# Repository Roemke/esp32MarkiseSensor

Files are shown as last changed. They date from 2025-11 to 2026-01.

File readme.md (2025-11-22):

# Markisensensoren
Ein wenig was zur schaltung

# Schaltung Windsensor
den habe ich noch nicht:
Dieser liefert 20 Pulse pro s bei 1,75m/s
wind, viel mit chatgpt gespielt, er liefert teilweise widersprüchliche

Schaltpläne, daher hier nochmal die mir sinnvoll erscheinende Variante
Windsensor: https://www.amazon.de/dp/B0872XPWFC?ref=ppx_yo2ov_dt_b_fed_asin_title
Mumusuki 0-70 m/s Umgebungssignal Ausgang Impulstyp Kohlenstoff 
Windgeschwindigkeitssensor Anemometer DREI Tassen Sender Windgeschwindigkeitssensor 

Erfahrung mit chat-GPT zur Schaltungskonzeption. Solange es um
Textbeschreibungen geht, hört es sch vernünftig an, wenn er daraus 
Schaltpläne macht (Ascii oder PNG) kommt ziemlich viel Müll heraus. 
Der folgende Plan müsste sinnvoll sein

```text
3.3V
     |
    4.7k  <-- Pull-up (zieht Signal auf 3.3V)
     |
     +------ Node_Signal ----+------> [1k] ----> GPIO (ESP32)
     |                      |
     |                     (optional)
     |                      | 
   Sensor OUT (open-col.)   --- C = 10 nF
     blau                   --- 
                            |
                            GND
```
Windsensor braucht 5-30 V separat und gemeinsame Masse mit ESP

Erläuterungen / wichtige Punkte

    Node_Signal ist der gemeinsame Punkt, an dem Pull-up, Sensor-OUT und Kondensator zusammentreffen.

    Sensor OUT ist open-collector / NPN: wenn aktiv → Node wird auf GND gezogen (LOW). 
    Wenn inaktiv → Pull-up zieht Node auf 3.3 V (HIGH).

    1 kΩ sitzt zwischen Node und dem ESP-GPIO (physisch nahe am ESP-Pin angebracht). 
    Er schützt den GPIO bei Fehlverdrahtung oder wenn der Pin versehentlich als Ausgang konfiguriert ist.

    C = 10 nF (optional) zwischen Node_Signal und GND dicht am ESP-Eingang: entstört sehr kurzzeitige Störungen, 
    aber klein genug, um keine 800 Hz-Impulse zu verschlucken (mit 4.7k → τ ≈ 47 µs).
    (Keramik-Kondensator)

    Gemeinsame Masse: Sensor-GND und ESP-GND unbedingt verbinden.

Strom-/Pegelrechnung (zur Sicherheit)

    Wenn Sensor LOW zieht: Strom durch Pull-up ≈ 3.3 V / 4.7 k ≈ 0.7 mA → unkritisch.

    Wenn aufgrund Boot/Fehlkonfig ein Pegelkonflikt entsteht (ESP Pin OUTPUT HIGH = 3.3 V, Sensor zieht auf GND), 
    begrenzt 1 k den Strom grob auf ~3.3 mA → schützt den Pin. (vorher war
    auch von Blitz und elektromagnetschen Störungen die Rede

Ich habe in Erinnerung, dass ich GPIO 33 gewählt habe. 

## Reedschalter Markise 
Die Reed-Schalter für die Markise (GPIO 26 m, 25 s1 und 27 s2)

Sie sind folgender Typ: 
https://www.amazon.de/dp/B07Z4NCWDD?ref=ppx_yo2ov_dt_b_fed_asin_title&th=1
normally closed, d.h. der magnet schließt das system (chat gpt sieht die
Bezeichnung genau anders herum) 

Schaltung ist vom GPIO 100nF Keramik auf GND (Entstörung) direkt am ESP pin
und 470Ohm in Serie im Signalleiter, als Schutz.
(bei der Windgeschichte ist es anders, da kommt erst der 1k Widerstand dann
der kondensator (vom esp aus gesehen), eine analyse durch chat gpt sagt aber
das auch dies ok ist, wobei bei der Windschaltung ja auch nicht der interne
pullup genutzt wird.
 
Hier wird kein externer pullup eingesetzt, da der Interne reicht. Dieser ist
relativ hochohmig 40-50k und zieht daher den GPIO nur langsam auf high, das
macht bei den Reeds für die markise aber nichts 

## Temperatur Luftfeuchtigkeit

Und dann noch ein dht22 engebaut in am2302 (hat nur 3 Beinchen) für
Temperatur und Luftfeuchtigkeit, ist direkt an GPIO angeschlossen (GPIO23)
und an 3.3V vom ESP

Stromversorgung ESP über USB, ansonsten alles auf einer Lochrasterplatine. 
Es würde sich aber ein PCB lohnen.

## Stand
Lötarbeiten auch für den Windsensor sind soweit durch. Blau für Signale der
Reedkontakte und des Temperatursensors verwendet, grün für Windsensor.
Alles auf Lochraster, schon eine ziemliche Bastelei, hier hätte sich ein
Platinendesign gelohnt, also machen, wenn es nicht stabil läuft.
Na ob ich dazu noch Lust habe? Die Verkabelung nach außen über Wagoklemmem
gemacht, es sind halt jetzt doch einige, eigenes kleines Gehäuse
3mal Reed - in 2er
3.3 V  - in 2er
Temp   - in 2er
Signal Wind - in 2er 
12 V   - in 3er (an Spannungswandler auf 5 V für Esp / an Windsensor / Eingang
Masse  - jede Menge, ich hoffe ich habe alles, an 5er Wago

den Temp-Sensor in eigenes kleines gehäuse, nicht gut, aber egal, kein Aufwand 
betreiben, der Sensor wird schon 1-2 Jahre halten :-), habe aber schwarzes pla genommen, bei
Sonne wird er gut warm werden...

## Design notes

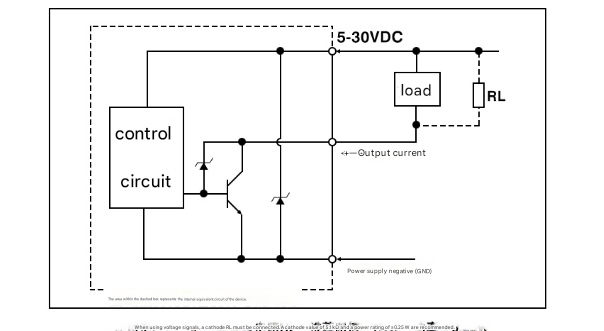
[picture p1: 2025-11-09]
SchaltplanNPN.png

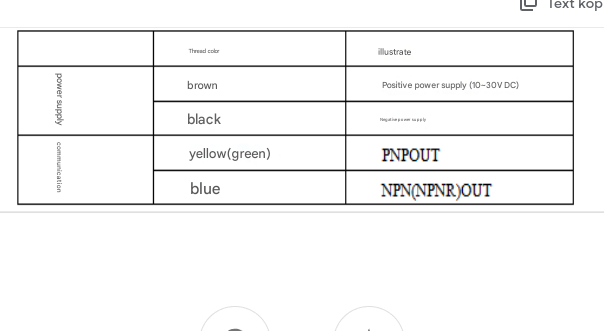
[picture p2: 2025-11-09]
WindsensorBelegung.png

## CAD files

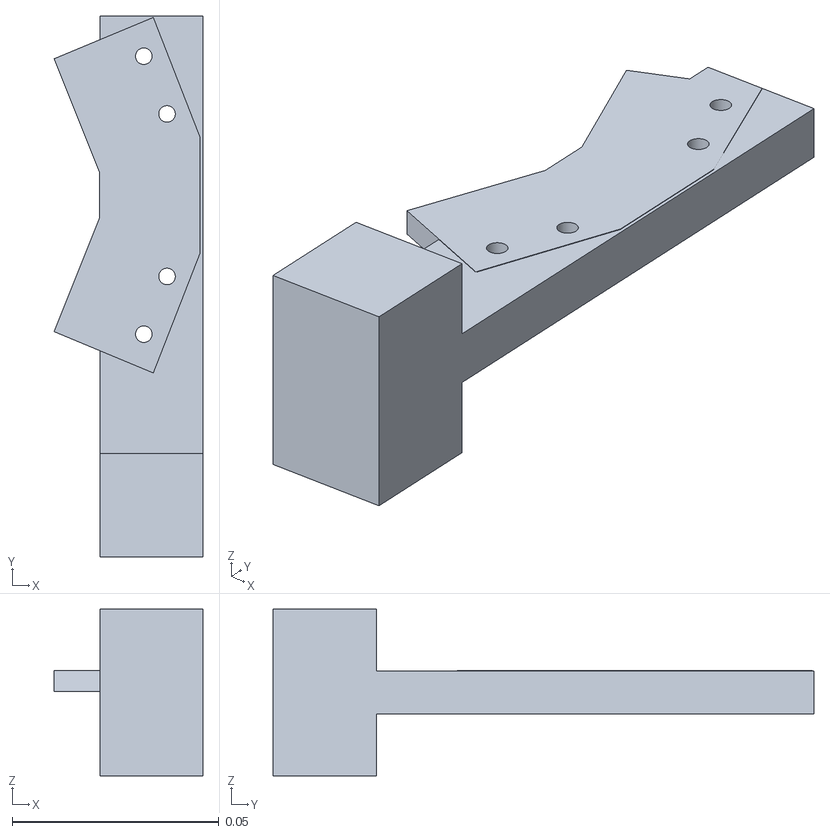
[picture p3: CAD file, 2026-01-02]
magnetHalter.stl
0.036 x 0.131 x 0.0404

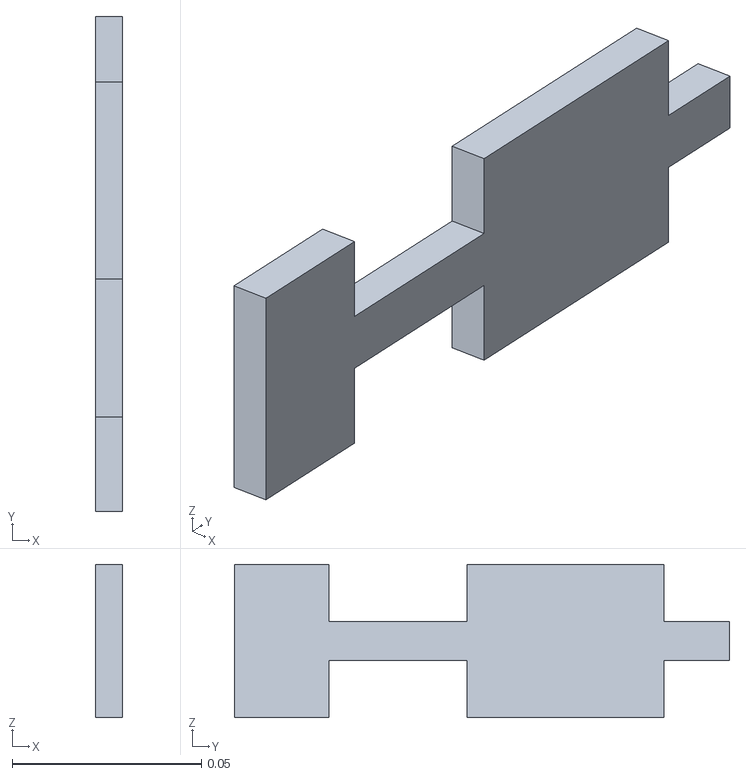
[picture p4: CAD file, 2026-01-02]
magnetHalterPlatte.stl
0.00703 x 0.131 x 0.0404

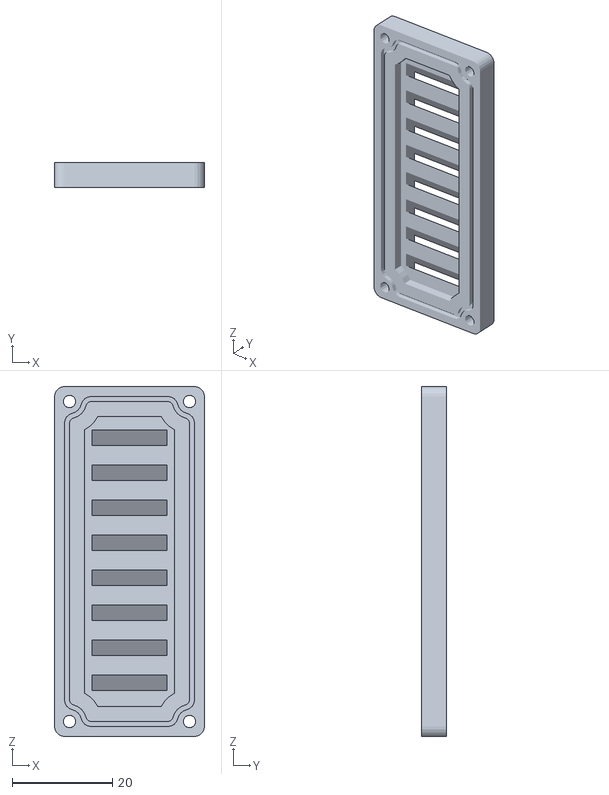
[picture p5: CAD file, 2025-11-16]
housing_sendor_dht22_cover.stl
30.0 x 5.00 x 70.0

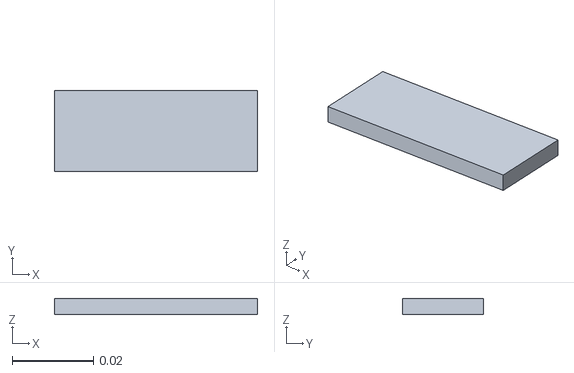
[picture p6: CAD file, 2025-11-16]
plate.stl
0.05 x 0.02 x 0.004

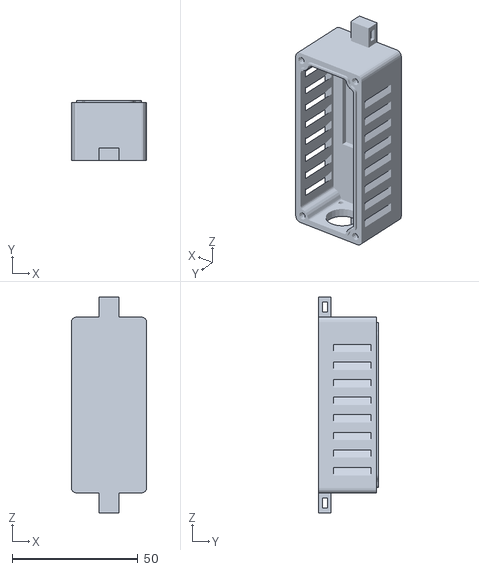
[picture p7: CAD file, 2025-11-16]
housing_sendor_dht22_body_outdoor_pg7.stl
30.0 x 23.9 x 86.0

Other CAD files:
magnetHalter.blend
plate.blend

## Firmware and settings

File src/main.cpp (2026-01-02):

//main.cpp

//#include <EEPROM.h> umgestellt auf littlefs
// Eigene Header
//#include "credentials.h" //fuer zuhause, eigentlich überflüssig mit wifi.h
#include "main.h"
#include "indexHtmlJS.h"
#include "wifi.h"
#include "logging.h"
#include "mqtt.h"
// Problem - chatgpt: 
// Du sendest WebSocket-Nachrichten (ws.textAll()) während eines WebSocket-Events.
//hmm, hätte ich auch selber drauf kommen können...?
// müsste ich ggf. auch in anderen Projekten anpassen...
bool pendingReboot = false;
bool insideWebSocketEvent = false;
//gleiches Problem bei informClients (json-kram)
std::vector<PendingWSMsg> wsOutbox;

// ---- WebServer + WebSocket ----
AsyncWebServer server(80);
AsyncWebSocket ws("/ws");
// DHT22 (AM2302)
DHTesp dht;
bool dhtReady = false;
float curTemp = NAN, curHum = NAN;
uint32_t lastDhtMs = 0;
static const char* REED_CFG_PATH = "/reed.json";


//fuer die reedPins
struct ReedPins {
  int markise = 26; // Defaults
  int s1 = 25;
  int s2 = 27; 
  int wind = 33;
  int t = 23;   // Temperatur, kein Reed, aber speichern
} reedPins;

//windgeschichten
volatile uint32_t windPulses = 0;   // Zählt die Pulse per ISR, volatile wegen ISR

float windSpeed = 0.0f; 

void IRAM_ATTR windISR() { //darf nicht inline sein
  windPulses++;
}

bool pollWindSensor() 
{
    static float lastWind = NAN;
    static uint32_t lastPoll = 0;

    uint32_t now = millis();
    if (now - lastPoll < 500) return false; // alle 500 ms
    lastPoll = now;

    // Pulse atomar lesen und zurücksetzen
    uint32_t pulses = windPulses;
    windPulses = 0;

    // 500ms → factor 2
    float pps = pulses * 2.0f;
    float newWind = pps * (1.75f / 20.0f);

    bool changed = false;
    if (isnan(lastWind) || fabsf(newWind - lastWind) >= 0.1f) {  
        // Änderung >= 0.1 m/s
        changed = true;
    }

    windSpeed = newWind;
    lastWind = newWind;

    if (changed) {
        logPrintf("Wind geändert: %.2f m/s\n", windSpeed);
    }

    return changed;
}


// Entprellung für Reedkontakte (aktiv LOW)
struct Debounce {
  int pin = -1;
  bool stable = false;   // entprellt (true = Reed geschlossen = LOW)
  bool lastRaw = false;
  uint32_t lastChange = 0;
  uint16_t debounceMs = 20;
} dbM, dbS1, dbS2;

static inline bool rawReed(int pin) { return digitalRead(pin) == LOW; }

bool updateDebounce(Debounce& d, uint32_t nowMs) {
  bool raw = rawReed(d.pin);
  bool changed = false;
  if (raw != d.lastRaw) { d.lastRaw = raw; d.lastChange = nowMs; }
  if ((nowMs - d.lastChange) >= d.debounceMs && d.stable != d.lastRaw) {
    d.stable = d.lastRaw;
    changed = true;
  }
  return changed;
}

// Sensor-Snapshot als JSON-String bauen
String makeSensorMsg() {
  JsonDocument doc;
  doc["action"] = "sensor";
  JsonObject v = doc["value"].to<JsonObject>();
  if (!isnan(curTemp)) v["t"] = curTemp;
  if (!isnan(curHum))  v["h"] = curHum;
  v["m"]  = (int)dbM.stable;
  v["s1"] = (int)dbS1.stable;
  v["s2"] = (int)dbS2.stable;
  v["w"]  = roundf(windSpeed * 10) / 10.0f;
  String msg;
  serializeJson(doc, msg);
  return msg;
}


static bool isSafeInputPullupPin(int gpio) {
  // verbotene Gruppen
  if (gpio >= 6 && gpio <= 11) return false;  // Flash
  if (gpio >= 34 && gpio <= 39) return false;  // keine internen Pullups
  if (gpio == 0 || gpio == 2 || gpio == 12 || gpio == 15) return false; // Boot-Straps
  // ansonsten ok (0..39)
  return gpio >= 0 && gpio <= 39;
} 
bool reedSaveConfig() {
  File f = LittleFS.open(REED_CFG_PATH, "w");
  if (!f) return false;
  JsonDocument doc;
  doc["markise"] = reedPins.markise;
  doc["s1"] = reedPins.s1;
  doc["s2"] = reedPins.s2;
  doc["t"] = reedPins.t;
  doc["wind"] = reedPins.wind;
  bool ok = (serializeJson(doc, f) > 0);
  f.close();
  return ok;
}

bool reedLoadConfig() {
  if (!LittleFS.exists(REED_CFG_PATH)) {
    // Defaults erstmal speichern
    return reedSaveConfig();
  }
  File f = LittleFS.open(REED_CFG_PATH, "r");
  if (!f) return false;
  JsonDocument doc;
  auto err = deserializeJson(doc, f);
  f.close();
  if (err) return false;

  int m = doc["markise"] | reedPins.markise;
  int s1 = doc["s1"] | reedPins.s1;
  int s2 = doc["s2"] | reedPins.s2;
  int t = doc["t"] | reedPins.t;
  int w = doc["wind"] | reedPins.wind;

  // Validieren
  if (isSafeInputPullupPin(m)) reedPins.markise = m;
  if (isSafeInputPullupPin(s1)) reedPins.s1 = s1;
  if (isSafeInputPullupPin(s2)) reedPins.s2 = s2;
  if (isSafeInputPullupPin(t)) reedPins.t = t;
  if (isSafeInputPullupPin(w)) reedPins.wind = w;
  return true;
}

void reedApplyPins() {
  pinMode(reedPins.markise, INPUT_PULLUP);
  pinMode(reedPins.s1, INPUT_PULLUP);
  pinMode(reedPins.s2, INPUT_PULLUP);
  pinMode(reedPins.t, INPUT);
  pinMode(reedPins.wind, INPUT); //externer Pullup
  attachInterrupt(reedPins.wind, windISR, FALLING);//interrupt ISR bei fallender Flanke
  
}

static void mqttPublishAwning() {
  JsonDocument doc;
  bool closed = dbM.stable;                 // dein Reed M als „geschlossen/offen“
  doc["closed"] = closed;
  // optional: alte Namenskompatibilität
  doc["m"] = closed ? "geschlossen" : "offen";
  // optional: S1/S2 als binäre Readings
  doc["s1"] = dbS1.stable ? 1 : 0;
  doc["s2"] = dbS2.stable ? 1 : 0;
  // optional: Prozent p, falls Du sie berechnen kannst
  // doc["p"] = isnan(percent) ? nullptr : (int)lroundf(constrain(percent,0,100));

  String payload; 
  payload.reserve(96);
  serializeJson(doc, payload);
  mqtt.publishAwningStatus(payload);        // -> awning/status
}

static void mqttPublishClimate() {
  JsonDocument doc;
  if (isnan(curTemp)) doc["t"] = nullptr;
  else                doc["t"] = roundf(curTemp * 10) / 10.0f;

  if (isnan(curHum))  doc["h"] = nullptr;
  else                doc["h"] = roundf(curHum * 10) / 10.0f;

  // Wind (m/s)
  if (isnan(windSpeed)) doc["w"] = nullptr;
  else                  doc["w"] = roundf(windSpeed * 10) / 10.0f;

  String payload; 
  payload.reserve(128);
  serializeJson(doc, payload);
  mqtt.publishClimateStatus(payload);       // -> climate/status
}


//Prozessor um ggf. Werte zu setzen (webseite)
String processor(const String& var)
{
  String result = "";
 
  if (var == "COPYRIGHT")
    result = "2025 by Roemke";
  else if (var == "WIFI_MAC_AP")
    result = wifiMacAp;
  else if (var == "WIFI_MAC_STA")
    result = wifiMacSta;
  else if (var == "WIFI_MAC_MODE")
    result = wifiMode;
  else if (var == "MQTT_BROKER")
    result = mqtt.broker;
  else if (var == "MQTT_PORT")
    result = String(mqtt.port);
  else if (var == "GPIO_MARKISE")
    result = String(reedPins.markise);
  else if (var == "GPIO_S1")
    result = String(reedPins.s1);
  else if (var == "GPIO_S2")
    result = String(reedPins.s2);
  else if (var == "GPIO_T")
    result = String(reedPins.t);
  else if (var == "GPIO_WIND")
    result = String(reedPins.wind);
    
  return result;
}



// ---- WebSocket Event Handler ----
// Nachricht an alle Clients senden
template <typename T>
void informClients(const String& action, T value) 
{
  JsonDocument doc;
  doc["action"] = action;
  doc["value"] = value;   // JsonVariant nimmt String oder int

  String msg;
  serializeJson(doc, msg);
  wsOutbox.push_back({0, msg});
}


void initialInformClient(AsyncWebSocketClient *client)
{  
  JsonDocument doc;
  doc["action"] = "init";
  // Log-Array hinzufügen
  JsonArray logArr = doc["logs"].to<JsonArray>();
  for (uint8_t i = 0; i < logCount; i++) {
    uint8_t idx = (logIndex + LOG_BUFFER_SIZE - logCount + i) % LOG_BUFFER_SIZE;
    logArr.add(logBuffer[idx]);
  }
  String msg;
  serializeJson(doc, msg);
  wsOutbox.push_back({client->id(), msg});
  wsOutbox.push_back({client->id(), makeSensorMsg()});
}

void onWsEvent(AsyncWebSocket *server, AsyncWebSocketClient *client,
  AwsEventType type, void *arg, uint8_t *data, size_t len)
{  
  insideWebSocketEvent = true;
  if (type == WS_EVT_CONNECT) 
  {
    logPrintf("📡 Client #%u verbunden\n", client->id());
    // Aktuellen Status senden
    initialInformClient(client);
    insideWebSocketEvent = false;
    return;
  }
  if (type == WS_EVT_DISCONNECT) {
    insideWebSocketEvent = false;
    return;
  }
  if(type != WS_EVT_DATA) 
  {
    insideWebSocketEvent = false;
    return;
  }

  logPrintf("Event-Type: %d, Heap: %d\n", type, ESP.getFreeHeap());
  AwsFrameInfo *info = (AwsFrameInfo*)arg;

  // Debug aller Bedingungen
  if(!info->final) {
      logPrintf("❌ WS: info->final == false\n");
      insideWebSocketEvent = false;
      return;
  }

  if(info->index != 0) {
      logPrintf("❌ WS: info->index = %u (erwartet 0)\n", info->index);
      insideWebSocketEvent = false;
      return;
  }

  if(info->len != len) {
      logPrintf("❌ WS: info->len (%u) != len (%u) -> frame fragmentiert?\n",
                info->len, len);
      insideWebSocketEvent = false;
      return;
  }

  if(info->opcode != WS_TEXT) {
      logPrintf("❌ WS: opcode = %u (erwartet WS_TEXT=1)\n", info->opcode);
      insideWebSocketEvent = false;
      return;
  }

  logPrintf("✔️ WS: Frame OK – Verarbeitung laeuft weiter\n");

  // StaticJsonDocument mit ausreichendem Puffer, deprecated sollte reichen ein JsonDocument zu nehmen
  JsonDocument doc;
  DeserializationError error = deserializeJson(doc, data,len);
  if(error) 
  {
    Serial.print("JSON Fehler: ");
    logPrintln(error.c_str());
    insideWebSocketEvent = false;
    return;
  }

  String action = doc["action"] | "";
  JsonVariant value = doc["value"];
  String valueStr = value.isNull() ? "" : value.as<String>();
  logPrintf("Aktion: %s, Wert: %s\n", action.c_str(), valueStr.c_str());
   
  if (action == "wifiSetCredentials")
  {
      String ssid = value["ssid"] | "";
      String pass = value["password"] | "";
      logPrintf("Neue WiFi Daten: SSID=%s, PASS=%s\n", ssid.c_str(), pass.c_str());
      if (ssid.length() > 0)
      {
          wifiSetCredentials(ssid.c_str(), pass.c_str());
          informClients("wifiState", "saved");
          pendingReboot = true;          
      }
  }
  else if (action == "mqttSet")
  {
      String broker = value["broker"] | "";
      int port = value["port"] | 1883;
      logPrintf("Neue MQTT Daten: BROKER=%s, PORT=%d\n", broker.c_str(), port);
      if (broker.length() > 0)
      {
          mqtt.broker = broker;
          mqtt.port = port;
          mqtt.saveConfig();          
          // Kein Neustart notwendig, MQTT-Verbindung wird neu initialisiert
      }
  }
  else if (action == "reedSetPins") 
  {
    int m  = value["markise"] | reedPins.markise;
    int s1 = value["s1"]      | reedPins.s1;
    int s2 = value["s2"]      | reedPins.s2;
    int t = value["t"]      | reedPins.t;
    int w  = value["wind"] | reedPins.wind;

    // Validieren
    if (!isSafeInputPullupPin(m) || !isSafeInputPullupPin(s1) || !isSafeInputPullupPin(s2)) {
      informClients("error", "Ungueltige GPIOs (keine Pullups/Flash/Bootstraps)");
      insideWebSocketEvent = false;
      return;
    }
    // Vorherige Pins sind INPUT_PULLUP – keine Deinit nötig,
    // optional könnte man hier prüfen, ob Pins sich geändert haben.
    reedPins.markise = m;
    reedPins.s1 = s1;
    reedPins.s2 = s2;
    reedPins.t = t;
    reedPins.wind = w;
    
    reedApplyPins();
    reedSaveConfig();
    informClients("reedPinsSaved", "ok");
    logPrintf("GPIO Pins aktualisiert: M=%d, S1=%d, S2=%d, T=%d, W=%d\n", m, s1, s2,t,w);
  }
  else if (action == "reboot") 
  {
    logPrintln("Reboot Befehl empfangen, Neustart...");
    informClients("rebooting", "ESP wird neu gestartet");
    pendingReboot = true;        
  }
  else if (action == "check") 
  {
    String msg = valueStr.length() > 0 ? valueStr : "Testnachricht vom Client";
    logPrintf("Check-Nachricht empfangen: %s\n", msg.c_str());
    informClients("check", msg);
  }
  else if (action == "setMaxWind")
  {
      int mw = value.as<int>();//esp benötigt den Wert nicht, verteilt aber an die Clients
      logPrintf("MaxWind setzen auf: %d\n", mw);
      // Rückmeldung an alle Clients
      informClients("setMaxWind", mw);      
  }
  
  insideWebSocketEvent = false;
}

void setupDHTandSensor()
{
    // Debouncer initialisieren
    dbM.pin = reedPins.markise;
    dbS1.pin = reedPins.s1;
    dbS2.pin = reedPins.s2;
    uint32_t now = millis();
    dbM.lastRaw = dbM.stable = rawReed(dbM.pin);
    dbS1.lastRaw = dbS1.stable = rawReed(dbS1.pin);
    dbS2.lastRaw = dbS2.stable = rawReed(dbS2.pin);
    dbM.lastChange = dbS1.lastChange = dbS2.lastChange = now;
  
    // DHT22 (AM2302) starten
    dht.setup(reedPins.t, DHTesp::DHT22);
    dhtReady = true;    
}

void setupOTA() {
  ElegantOTA.begin(&server); // Startet ElegantOTA  
  
  ElegantOTA.onStart([]() {
    logPrintln("OTA Start");
  });

  ElegantOTA.onEnd([](bool success) {
    success ? logPrintln("OTA Ende, Neustart...") : logPrintln("OTA Ende mit Fehler");
    success ? ESP.restart() : logPrintln("Kein Neustart");   
  });

  ElegantOTA.onProgress([](unsigned int progress, unsigned int total) {
    char buf[64];
    snprintf(buf, sizeof(buf), "OTA Fortschritt: %u/%u", progress, total);
    logPrintln(buf);
    informClients("ota", buf);
  });
  
  logBufferAdd("🌐 OTA Update verfügbar unter /update");
}

void setupWebsocket()
{
  // WebSocket einbinden
  ws.onEvent(onWsEvent);
  server.addHandler(&ws);

  // lustig, ich bin alt,  [] leitet einen Lambda Ausdruck ein, also eine anonyme Funktion
  // die gabs frueher nicht :-), dafür mehr Lametta
  server.on("/favicon.ico", [](AsyncWebServerRequest *request)
            {
              request->send(204); // no content
            });

  // Hauptseite
  server.on("/", HTTP_GET, [](AsyncWebServerRequest *request)
            { request->send(200, "text/html", index_html, processor); });
  //jsonDaten abfragen - liefert hier zunächst letzter Stand, später evtl. reedKontakt abfragen
  server.on("/getData", HTTP_GET, [](AsyncWebServerRequest *request)
            {
              JsonDocument doc;
              doc["status"] = "ok";
              String response;
              serializeJson(doc, response);
              request->send(200, "application/json", response);
            });
}

//folgendes nicht mehr benötigt, da kein Befehl empfangen wird
/*
void onMqttCommand(const String& cmd)
{
    logPrintf("MQTT Befehl empfangen: %s\n", cmd.c_str());
}
*/
void statusPoll() {
  uint32_t now = millis();

  // Awning: Änderungen separat erfassen
  bool awnChanged = false;
  awnChanged |= updateDebounce(dbM,  now);
  awnChanged |= updateDebounce(dbS1, now);
  awnChanged |= updateDebounce(dbS2, now);

  // Klima: Änderungen mit Hysterese erfassen
  bool cliChanged = false;
  if (dhtReady && (now - lastDhtMs) >= 2000) {
    lastDhtMs = now;
    TempAndHumidity th = dht.getTempAndHumidity();
    if (!isnan(th.temperature) && !isnan(th.humidity)) {
      bool tChanged = isnan(curTemp) || fabsf(th.temperature - curTemp) >= 0.1f;
      bool hChanged = isnan(curHum)  || fabsf(th.humidity    - curHum)  >= 0.1f;
      if (tChanged) curTemp = th.temperature;
      if (hChanged) curHum  = th.humidity;
      cliChanged = (tChanged || hChanged);
    }
  }

  // Windsensor abfragen
  bool windChanged = pollWindSensor();

  // WebSocket wie gehabt
  if (awnChanged || cliChanged || windChanged) {
    ws.textAll(makeSensorMsg());
  }

  // MQTT: getrennt publizieren
  if (awnChanged) mqttPublishAwning();  
  if (cliChanged || windChanged) mqttPublishClimate();
}

 
 
void processWSOutbox() {
  if (wsOutbox.empty()) return;

  for (auto &item : wsOutbox) {
      if (item.clientId == 0) {
          ws.textAll(item.msg);
      } else {
          AsyncWebSocketClient *c = ws.client(item.clientId);
          if (c && c->status() == WS_CONNECTED) {
              c->text(item.msg);
          }
      }
  }
  wsOutbox.clear();
}


// ---- Setup und Loop ----     
void setup()
{
  Serial.begin(115200);
  if (!LittleFS.begin(true)) { // true = bei Bedarf formatieren
    Serial.println("LittleFS mount failed");
    while (true) { delay(1000); }
  }
  wifiSetup();

  // OTA einrichten
   setupOTA();

   setupWebsocket();

   server.begin();
   logPrintln("HTTP-Server gestartet");

   // MQTT initialisieren
    mqtt.loadConfig();
    mqtt.begin();    
   //mqtt.setOnCmd(onMqttCommand); // keine Befehle vom MQTT-Server
   // Reed-Pins laden und anwenden
    reedLoadConfig();
    reedApplyPins();  
    setupDHTandSensor();
}

void loop() 
{
  
  ws.cleanupClients();
  //ElegantOTA.loop(); nur wenn blockierend, hier nicht nötig da Async

  statusPoll();
  mqtt.poll();
  if (pendingReboot && pendingMessages.empty() && !insideWebSocketEvent)
  {
    delay(200);     // kleine Chance für Clients zum Empfangen
    ESP.restart();  // jetzt erst rebooten
  }
  //interessant, hier kein insideWebSocketEvent nötig
  processWSOutbox();
  logProcessPending();
}

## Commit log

2025-11-16 Fehlersuche / Korrektur, ein paar verwendete druckdateien dazu
    [housing_sendor_dht22_body_outdoor_pg7.stl, housing_sendor_dht22_cover.stl, plate.blend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]
2025-11-22 Wind so weit durch, lasse es jetzt dabei, Sensoren für markisenpos fehlen noch
2026-01-02 Logging etwas überarbeitet, WS comm etwas überarbeitet (evtl. Stabilität, nicht aufgepasst) blender Dateien dazu, sie sind aber nicht gut und nur für mich geeignet Hilfe angepasst
    [magnetHalter.blend, magnetHalter.stl, magnetHalterPlatte.stl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]
